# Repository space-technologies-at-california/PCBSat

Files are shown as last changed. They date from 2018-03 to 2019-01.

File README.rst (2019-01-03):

=============
PCB Satellite
=============
Space Technologies at Cal (https://stac.berkeley.edu)

University of California, Berkeley

Getting Started
===============
Clone this repository. Then:

Eagle
-----
#. Obtain the `STAC Eagle library <https://github.com/space-technologies-at-california/electronics>`_ by running::
   
    git submodule init
    git submodule update

#. `Add the library to Eagle <https://www.instructables.com/id/Adding-a-Library-to-Eagle-CAD/>`_.

Firmware
--------
#. Install `MSP430-GCC <http://www.ti.com/tool/msp430-gcc-opensource>`_ and
   `MSPDebug <https://dlbeer.co.nz/mspdebug/>`_.

#. In *firmware/*, make a new file called *msp430.mk.inc* and specify the path
   to your MSP430-GCC installation. For example::

    MSP430_TOOLCHAIN=/usr/local/gcc-msp430-ti-toolchain-5.01.02.00

#. Run ``make`` from *firmware/* to build all firmware configurations. To
   build a specific configuration, change to the appropriate subdirectory (for
   example, *debug/*) and run ``make``. If ``make`` complains about a missing
   *gitrev.h*, type ``make gitrev.h`` and re-run.

#. To change a build configuration, edit *config.h* in the appropriate
   subdirectory.

Programming
~~~~~~~~~~~
#. Obtain a programmer. We use the MSP430F5529 LaunchPad to program our sprite
   using Spy-Bi-Wire (SBW), but any SBW-compatible programmer should work.

#. Disconnect the 5V, 3V, GND, SBW RST and TST jumpers from the LaunchPad.

#. Connect the 3V, GND, SBW RST and TST jumpers on the ezFET-lite side to the
   target.

#. Run ``make prog`` to program, and run ``make verify`` to read back what was
   programmed.

Simulation
----------
Dependencies: igrf12 (https://github.com/scivision/igrf12)

#. Run ``python3 pull_iss_locdata.py``. This will collect (timestamp, latitude,longitude) data of the ISS for 9 hours at 10 second increments. This will create an output file in the current directory titled ``iss_loc_data_{timestamp}.csv``.  
#. Run ``python3 data_gen.py -f iss_loc_data_{timestamp}.csv`` where timestamp corresponds to the file created in the previous step. This will create an output file in the current directory that contains magnetometer data (x,y,z), gyrometer data (x,y,z), and the expected axis and power that the PCBSat should rotate along in addition to the file's previous contents. This output file will be titled ``full_{timestamp}.csv``. The units for the magnetometer data are Gauss and the units for the gyrometer data are radians/second.  

The models for predicting power and axis are still in progress. 

To run tensorboard, navigate to /simulations/python/ and execute `tensorboard --logdir="tmp/model/"`. Make sure that you have the most recent versions of tensorflow and tensorboard installed. 

Directory Structure
===================
- ./eagle : Contains all necessary Eagle files for the sprite board

  - ./eagle/sprite-test: Contains the version of the sprite manufacture by 
    Bay Area Circuits as a test board. It is largely based on the sprite
    verison created by Zac Manchester here: https://github.com/kicksat/sprite

  - ./eagle/final-sprite: Contains the version of the sprite we are currently
    working on. Our sprite began from the attitude-sprite designed by Zac
    Mancherster here: https://github.com/kicksat/attitude-sprite

  - ./eagle/electronics: STAC Eagle library submodule. See Eagle_. Please add
    any parts to the stac.lbr file contained there.
    
- ./simulation : Contains all the simulation netlists and other data 

- ./firmware : Contains all the firmware for the sprite

- ./gerbers : Contains the gerbers for the sprites. 

`Getting Started with Sprite Development Kit <https://github.com/kicksat/sprite/wiki/Getting-started-with-the-Sprite-Development-Kit>`_

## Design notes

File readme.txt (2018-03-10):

PCB Satellite
Space Technologies at Cal
University of California, Berkeley

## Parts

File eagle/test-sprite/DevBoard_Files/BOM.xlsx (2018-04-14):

Part | Value | Device | Package | Desicription | DigiKey Part Number | Manufacturer Part Number | Price | Link
C1 | 27pF | CAP0603-CAP | 0603-CAP | Capacitor | 399-1054-1-ND | C0603C270J5GACTU
C2 | 27pF | CAP0603-CAP | 0603-CAP | Capacitor | 399-1054-1-ND | C0603C270J5GACTU
C3 | 470nF | CAP0603-CAP | 0603-CAP | Capacitor | 399-3114-1-ND | C0603C474K8PACTU
C4 | 470nF | CAP0603-CAP | 0603-CAP | Capacitor | 399-3114-1-ND | C0603C474K8PACTU
C5 | 2.2nF | CAP0603-CAP | 0603-CAP | Capacitor | 399-1085-1-ND | C0603C222K5RACTU
C6 | 100nF | CAP0603-CAP | 0603-CAP | Capacitor | 399-5089-1-ND | C0603C104K5RACTU
C7 | 10nF | CAP0603-CAP | 0603-CAP | Capacitor | 399-1091-1-ND | C0603C103K5RACTU
C8 | 2.2nF | CAP0603-CAP | 0603-CAP | Capacitor | 399-1085-1-ND | C0603C222K5RACTU
C9 | 100nF | CAP0603-CAP | 0603-CAP | Capacitor | 399-5089-1-ND | C0603C104K5RACTU
C10 | 10nF | CAP0603-CAP | 0603-CAP | Capacitor | 399-1091-1-ND | C0603C103K5RACTU
C11 | 100nF | CAP0603-CAP | 0603-CAP | Capacitor | 399-5089-1-ND | C0603C104K5RACTU
C12 | 220nF | CAP0603-CAP | 0603-CAP | Capacitor | 399-1102-1-ND | C0603C224Z4VACTU
C13 | 4.7uF | CAP0603-CAP | 0603-CAP | Capacitor | 399-3482-1-ND | C0603C475K9PACTU
L1 | 12nH | INDUCTOR | 0603-INDUCTOR | Inductor | 587-1546-1-ND | HK160812NJ-T
LED1 | LED0603 | LED-0603 | 0603-LED | Chip LED | 475-2709-1-ND | LG L29K-G2J1-24-Z
R1 | 56K | RESISTOR0603-RES | 0603-RES | Resistor | P56.0KHCT-ND | ERJ-3EKF5602V
R2 | 47K | RESISTOR0603-RES | 0603-RES | Resistor | P47.0KHCT-ND | ERJ-3EKF4702V
R3 | 4.7K | RESISTOR0603-RES | 0603-RES | Resistor | P4.70KHCT-ND | ERJ-3EKF4701V
R4 | 4.7K | RESISTOR0603-RES | 0603-RES | Resistor | P4.70KHCT-ND | ERJ-3EKF4701V
R5 | 270R | RESISTOR0603-RES | 0603-RES | Resistor | P270GCT-ND | ERJ-3GEYJ271V
R6 | 0R | RESISTOR0805-RES | 0805-RES | Resistor | P0.0ACT-ND | ERJ-6GEY0R00V
R7 | 0R | RESISTOR0805-RES | 0805-RES | Resistor | P0.0ACT-ND | ERJ-6GEY0R00V
S1 | TASC | TASC | TASC | Triangular Advanced Solar Cell | N/A | N/A
S2` | TASC | TASC | TASC | Triangular Advanced Solar Cell | N/A | N/A
U1 | CC430F5137 | CC430F513X---RGZ48 | QFN-48 | MSP430 w/ Integrated Radio | 296-27420-1-ND | CC430F5137IRGZR | 6.59 | https://www.digikey.com/products/en?keywords=296-27420-1-ND
U2 | HMC5883LSMD | MMC5883MA | 16-LGA | 3-Axis Digital Compass | 1267-1072-1-ND | MMC5883MA | 5.47 | https://www.digikey.com/product-detail/en/memsic-inc/MMC5883MA/1267-1072-1-ND/7063085
U3 | ITG-3200 | ITG-3200 | QFN-24 | 3-Axis Gyroscope | 37T8091 (Newark) | ITG-3200 | 14.45 | http://www.newark.com/invensense/itg-3200/gyroscope-mems-triple-axis-qfn/dp/37T8091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
X1 | 26MHz | ABM11-XTAL | ABM11_CERAMIC_SMD_CRYSTALABM11 | Quartz Crystal | 535-9815-1-ND | ABM11-26.000MHZ-B7G-T | 1.68 | https://www.digikey.com/products/en?keywords=535-9815-1-ND
JP1 | DNP | Fair-Rite Ferrite Rod | n/a | Ferrite Rod | 623-4052077111 (Mouser) | 4052077111 | 0.16 | https://www.mouser.com/ProductDetail/Fair-Rite/4052077111
JP2 | DNP
JP3 | DNP | DNP | DNP | Jumper
JP4 | DNP | DNP | DNP | Jumper
 |  | DNP | DNP | Jumper
 |  | DNP | DNP | Jumper

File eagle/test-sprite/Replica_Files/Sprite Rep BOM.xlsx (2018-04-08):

Reference | Quantity | Manufacturer | Part Number | Package | Description | Type
C1, C2 | 2 | Kemet | C0603C270J5GACTU | 0603 | Cap 27 pF | DNS
C3, C4 | 2 | Kemet | C0603C474K8PACTU | 0603 | Cap 470 nF | SMT
C5 | 1 | Yageo | CC0603KRX7R9BB222 | 0603 | Cap 2.2 nF | SMT
C6 | 1 | Panasonic |  | 0603 | Cap 100 nF | DNS
C7 | 1 | Panasonic |  | 0603 | Cap 10 nF | DNS
L1 | 1 | Taiyo Yuden | HK160812NJ-T | 0603 | Inductor 32 nH | DNS
R1 | 1 | Panasonic | ERJ-3EKF5602V | 0603 | Resistor 56K | SMT
R2 | 1 | Panasonic | ERJ-3EKF4702V | 0603 | Resistor 47K | SMT
R3, R4, R5, R6, R7, R8 | 6 | Panasonic | ERJ-3GEYJ271V | 0603 | Resistor 270R | SMT
D1, D2, D3, D4, D5, D6 | 6 | Osram | LG L29K-G2J1-24-Z | 0603 | LED | SMT
S1 | 1 | Spectrolab |  | TASC | Soalar Cell | DNS
U1 | 1 | Texas Instruments | CC430F5137IRGZR | 48-QFN | MCU/Radio SoC | Fine Pitch
X1 | 1 |  |  | ABM11 | Crystal 26MHz | DNS

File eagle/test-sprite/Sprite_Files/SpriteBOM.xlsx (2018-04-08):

Part | Quantity | Value | Device | Package | Description | DigiKey Part Number
C1, C5, C7 | 3 | 10 nF | CAP0603-CAP | 0603-CAP | CAP CER 10000PF 50V X7R 0603 | 399-1091-1-ND
C2, C3 | 2 | 470nF | CAP0603-CAP | 0603-CAP | CAP CER 0.47UF 10V X5R 0603 | 399-3114-1-ND
C4 | 1 | 2.2nF | CAP0603-CAP | 0603-CAP | CAP CER 2200PF 50V X7R 0603 | 399-1085-1-ND
C6, C8, C9 | 3 | 0.1uF | CAP0603-CAP | 0603-CAP | CAP CER 0.1UF 50V X7R 0603 | 399-5089-1-ND
C10 | 1 | 10uF | CAP0603-CAP | 0603-CAP | CAP CER 10UF 10V X5R 0603 | 490-10475-1-ND
D1 | 1 | LED | LED0603-LED | 0603-LED | LED GREEN DIFFUSED 0603 SMD | 475-2709-1-ND
L1 | 1 | 12 nH | INDUCTOR0603 | 0603-IND | FIXED IND 12NH 300MA 280 MOHM | 587-1546-1-ND
P1, P2 | 2 | SPRITE_PIN | SPRITE_PIN | SPRITE_PIN | TESTPOINT PIN SMD | ED1088CT-ND
R1 | 1 | 56K | RESISTOR0603-RES | 0603-RES | RES SMD 56K OHM 1% 1/10W 0603 | P56.0KHCT-ND
R2 | 1 | 47K | RESISTOR0603-RES | 0603-RES | RES SMD 47K OHM 1% 1/10W 0603 | P47.0KHCT-ND
R3, R4, R6, R7 | 4 | 0R | RESISTOR0805-RES | 0805-RES | RES SMD 0.0 OHM JUMPER 1/8W 0805 | P0.0ACT-ND
R5 | 1 | 270R | RESISTOR0603-RES | 0603-RES | RES SMD 270 OHM 5% 1/10W 0603 | P270GCT-ND
S1, S2, S3, S4 | 4 | TRISOLX-WING | TRISOLX-WING | TRISOLX-T01 | Solar Cell TRISOLX | N/A
U1 | 1 | CC430F5137 | CC430F513X---RGZ48 | RGZ48 | IC MCU 16B 32K W/RF CORE 48VQFN | 296-38903-2-ND
U2 | 1 | LSM9DS1 | LSM9DS1 | LGA24-8X4 | ACCELEROMETER 3D INEMO 24TFLGA | 497-14946-1-ND
X1 | 1 | TCXO_7Z | TCXO_7Z | TXC_7Z | OSC TCXO 26.000MHZ CLPD SNWV SMD | 887-1622-1-ND

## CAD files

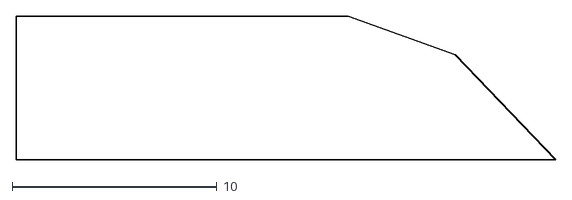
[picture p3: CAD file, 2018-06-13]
mechanical/TrisolX RS.dxf
26.4 x 7.04

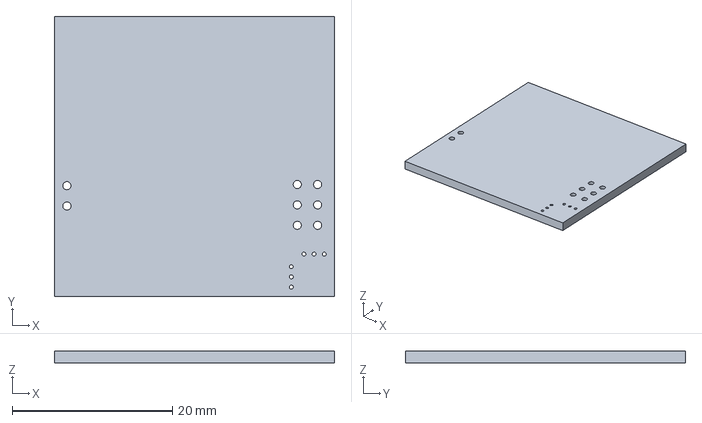
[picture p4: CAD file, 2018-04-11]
mechanical/DevBoard_stp.step
35.0 x 35.0 x 1.55 mm

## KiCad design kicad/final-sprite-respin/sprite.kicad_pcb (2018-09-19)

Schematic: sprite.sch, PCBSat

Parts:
A1, A2: SPRITEANTENNA_ANTENNA
C1, C7: 470n; C0402
C2: 2.2n; C0402
C3, C5, C15: 0.1u; C0402
C4, C6, C9, C11: 10n; C0402
C8, C12, C16, C17: 10u; C0402
C10, C18, C19, C20, C21, C22, C23, C24, C25, C26, C27, C28, C29, C30, C31, C32, C33: CPH3225A; CAPCP3225X100N
C13, C14: 4.7u; C0402
J1: M20-7910442R
L1: LPS4018-223M
L2: 12 nH; 0603
L3, L4: PCBSAT-TORQUECOIL
LED1: LED0603; LED-0603
MK1: Mounting_Hole
R1: 43K; R0402
R2: 270R; R0402
R3, R5, R6: 10K; R0402
R4: 56K; R0402
R7: 150K; R0402
R8: 1M; R0402
R9: 7K; R0402
R10: 200k; R0402
R11, R12, R22: 15R; R0402
R13, R14: OPT; R0402
R15: 5.49M; R0402
R16: 453K; R0402
R17: 4.53M; R0402
R18, R19: 5M; R0402
R20: 4.42M; R0402
R21: 5.6M; R0402
U1: CC430F513X; TI_MSP430_V16_RGZ48
U2: LSM9DS1; LGA24-8X4
U3: SPRITETCXO_TCXO_7Z; SPRITETCXO_TXC_7Z
U4, U6, U7: DRV8837; SON50P200X200X75-8N
U5: ADP5092; QFN50P400X400X100-25N
U8, U9: TASC
X1, X2: SPRITEPIN_SPRITE_PIN

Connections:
/DRDY: U1.11, U2.9
/DSW: U1.24, U5.22
/EN_1: U1.43, U4.7
/EN_2: U1.44, U6.7
/EN_3: U1.48, U7.7
/INT1: U1.4, U2.11
/INT2: U1.3, U2.12
/PGOOD: U1.12, U5.19
/PWM1: U1.1, U4.6, U6.6, U7.6
/PWM2: U1.2, U4.5, U6.5, U7.5
/REF: R15.2, R18.2, R20.2, U5.1
/REGGOOD: U1.37, U5.11
/REG_D0: U1.13, U5.24
/REG_D1: U1.15, U5.23
/RF_N: A1.IN1, A1.IN2, A1.IN3, U1.30
/RF_P: A2.IN1, A2.IN2, A2.IN3, U1.29
/SCL: R3.2, U1.9, U2.2
/SDA: R5.2, U1.10, U2.4
/SETHYS: R16.1, R17.2, U5.6
/SETPG: R15.1, R16.2, U5.5
/SETSD: R18.1, R19.2, U5.2
/SPIRAL: R22.1, U7.2
/SWN: L1.P$2, U5.13
/TERM: R20.1, R21.2, U5.4
/TST: J1.3, U1.39
/UART_RX: J1.5, U1.6
/UART_TX: J1.4, U1.5
/VBAT: C10.1 (+), C18.1 (+), C19.1 (+), C20.1 (+), C21.1 (+), C22.1 (+), C23.1 (+), C24.1 (+), C25.1 (+), C26.1 (+), C27.1 (+), C28.1 (+), C29.1 (+), C30.1 (+), C31.1 (+), C32.1 (+), C33.1 (+), U5.17
/VCORE: C1.1, U1.7
/~RST: C2.2, J1.2, R1.2, U1.40
GND: C1.2, C2.1, C3.2, C4.2, C5.2, C7.2, C8.2, C9.2, C10.2 (-), C11.2, C12.2, C13.2, C14.2, C15.2, C16.2, C17.2, C18.2 (-), C19.2 (-), C20.2 (-), C21.2 (-), C22.2 (-), C23.2 (-), C24.2 (-), C25.2 (-), C26.2 (-), C27.2 (-), C28.2 (-), C29.2 (-), C30.2 (-), C31.2 (-), C32.2 (-), C33.2 (-), J1.6, LED1.C, R4.2, R8.1, R9.2, R10.1, R17.1, R19.1, R21.1, U1.42, U1.TP, U2.14, U2.15, U2.16, U2.17, U2.18, U2.19, U2.20, U3.GND1, U3.GND2, U4.4, U4.9, U5.3, U5.7, U5.12, U5.25, U6.4, U6.9, U7.4, U7.9, U8.MINUS1, U8.MINUS2, U9.MINUS1, U9.MINUS2, X2.PIN
unnamed: C4.1, U2.21
unnamed: C5.1, U2.24
unnamed: C6.1, U1.25
unnamed: C6.2, U3.OUT
unnamed: C9.1, U5.8
unnamed: L3.1, U4.3
unnamed: L3.2, R11.2
unnamed: L4.1, R12.2
unnamed: L4.2, U6.3
unnamed: LED1.A, R2.2
unnamed: R2.1, U1.14
unnamed: R4.1, U1.33
unnamed: R6.2, U2.5, U2.6, U2.7, U2.8, U2.13
unnamed: R7.1, R8.2, U5.9
unnamed: R9.1, U5.20
unnamed: R10.2, U5.21
unnamed: R11.1, U4.2
unnamed: R12.1, U6.2
unnamed: R22.2, U7.3
VCC: C3.1, C14.1, C15.1, J1.1, L2.1, R1.1, R3.1, R5.1, R6.1, R13.2, R14.1, U1.8, U1.22, U1.41, U1.45, U2.1, U2.3, U2.22, U2.23, U4.8, U5.16, U6.8, U7.8, X1.PIN
VCCA: C7.1, C11.1, L2.2, U1.27, U1.28, U1.31, U1.32, U1.34, U3.VCC
VCCINT: C17.1, L1.P$1, R7.2, R14.2, U5.10, U8.PLUS, U9.PLUS
VCCIO: C8.1, C12.1, C13.1, C16.1, R13.1, U4.1, U5.14, U5.15, U6.1, U7.1

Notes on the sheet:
Sensing:
CORE:
Torque Coils
Power
REG_OUT = VCCIO = 1.5V (see Table 7) VSYS = VBAT = 2.2-2.7V
16 V
1% REQ
All Caps 3.3V Except C21 (16V) All Passives 0402 All Passives (5%) Except R4, R15 - R21 (1%) Subject to Change R2, R11, R12, R22 R7, R8 C3 MPPT Max efficiency: R7/(R7 + R8) = 87% Vsetsd: 1V*(1+R18/R19) = 2V Vbat_term: (3/2)V*(1+R20/R21) = 2.7V Vsetpg_falling: 1V*(1+(R15/(R16+R17))) = 2.102V Vsetpg_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
Design Notes
PCB Spiral Inductor Layers 2 and 3

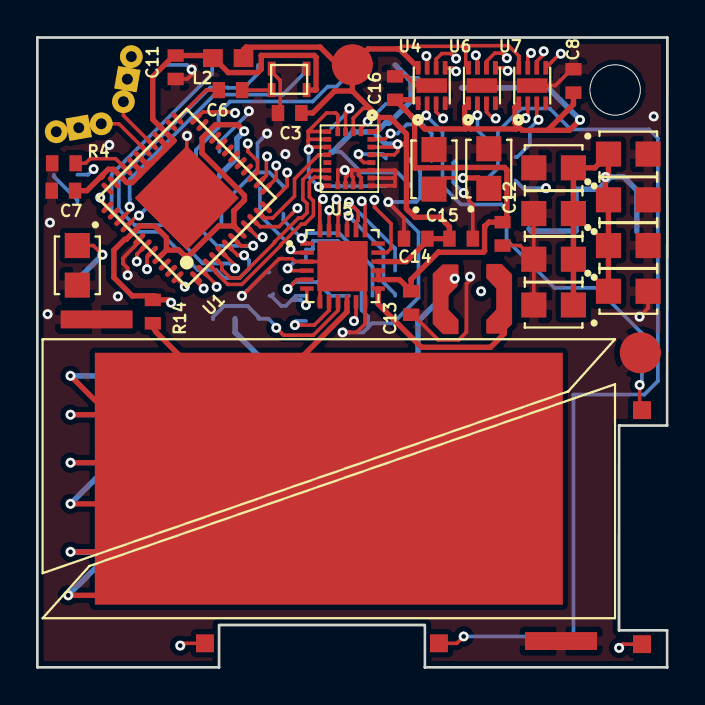
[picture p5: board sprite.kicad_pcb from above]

Board: 4 copper layers, 35.0 x 35.0 mm, 75 parts (0 on the bottom side), 54 nets.

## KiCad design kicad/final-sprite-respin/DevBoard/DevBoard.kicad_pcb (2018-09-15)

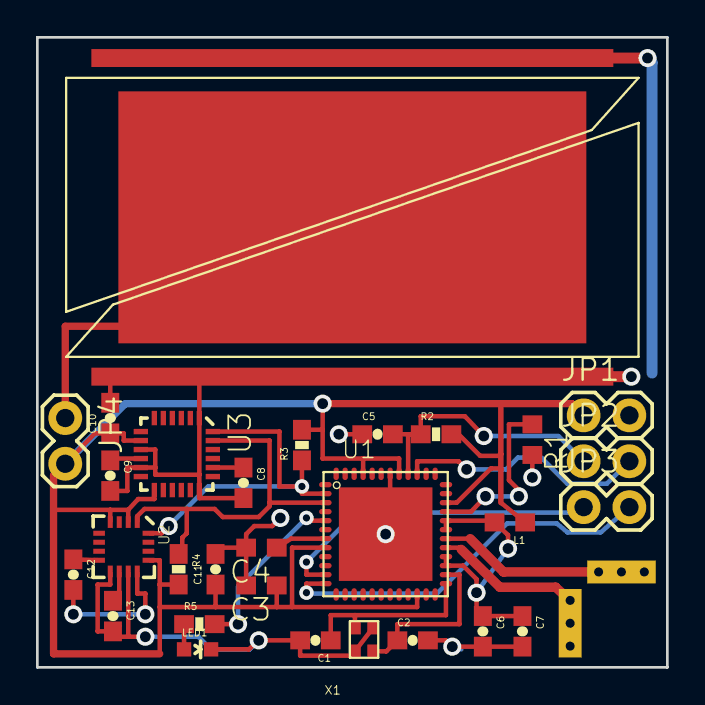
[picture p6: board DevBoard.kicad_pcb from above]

Board: 16 copper layers, 35.0 x 35.0 mm, 31 parts (0 on the bottom side), 23 nets.

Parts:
ANT-N1: ANTENNA
ANT-P1: ANTENNA
C1, C2: 27pF; 0603-CAP
C3, C4: 470nF; C0603
C5, C8: 2.2nF; 0603-CAP
C6, C9, C11: 100nF; 0603-CAP
C7, C10: 10nF; 0603-CAP
C12: 220nF; 0603-CAP
C13: 4.7uF; 0603-CAP
JP1, JP2, JP3, JP4: M02PTH; 1X02
L1: 12 nH; 0603
LED1: LED0603; LED-0603
R1: 56K; R0603
R2: 47K; 0603-RES
R3, R4: 4.7K; 0603-RES
R5: 270R; 0603-RES
S1: TASC
U1: CC430F5137; RGZ48
U2: HMC5883LSMD; 16LPCC
U3: ITG-3200; QFN-24
X1: 26 MHz; ABM11_CERAMIC-SMD-CRYSTAL

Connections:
/SCL: R4.1, U1.3, U2.1, U3.23
/SDA: R3.1, U1.2, U2.16, U3.24
GND: C1.2, C2.2, C3.2, C4.2, C5.1, C6.2, C7.2, C8.2, C9.2, C10.2, C11.2, C13.2, JP1.2, LED1.C, R1.2, S1.MINUS1, S1.MINUS2, U1.42, U1.TP, U2.9, U2.11, U3.1, U3.9, U3.11, U3.18, X1.P$2, X1.P$4
unnamed: ANT-N1.IN1, ANT-N1.IN2, ANT-N1.IN3, U1.30
unnamed: ANT-P1.IN1, ANT-P1.IN2, ANT-P1.IN3, U1.29
unnamed: C1.1, U1.25, X1.P$1
unnamed: C2.1, U1.26, X1.P$3
unnamed: C4.1, U1.7
unnamed: C5.2, JP2.1, R2.1, U1.40
unnamed: C6.1, C7.1, L1.2, U1.27, U1.28, U1.31, U1.32
unnamed: C8.1, U3.20
unnamed: C9.1, U3.10
unnamed: C12.1, U2.8
unnamed: C12.2, U2.12
unnamed: C13.1, U2.10
unnamed: JP2.2, U1.39
unnamed: JP3.1, U1.11
unnamed: JP3.2, U1.12
unnamed: JP4.1, S1.PLUS
unnamed: LED1.A, R5.1
unnamed: R1.1, U1.33
unnamed: R5.2, U1.5
VCC: C3.1, C10.1, C11.1, JP1.1, JP4.2, L1.1, R2.2, R3.2, R4.2, U1.8, U1.22, U1.34, U1.41, U1.45, U2.2, U2.4, U2.13, U3.8, U3.13

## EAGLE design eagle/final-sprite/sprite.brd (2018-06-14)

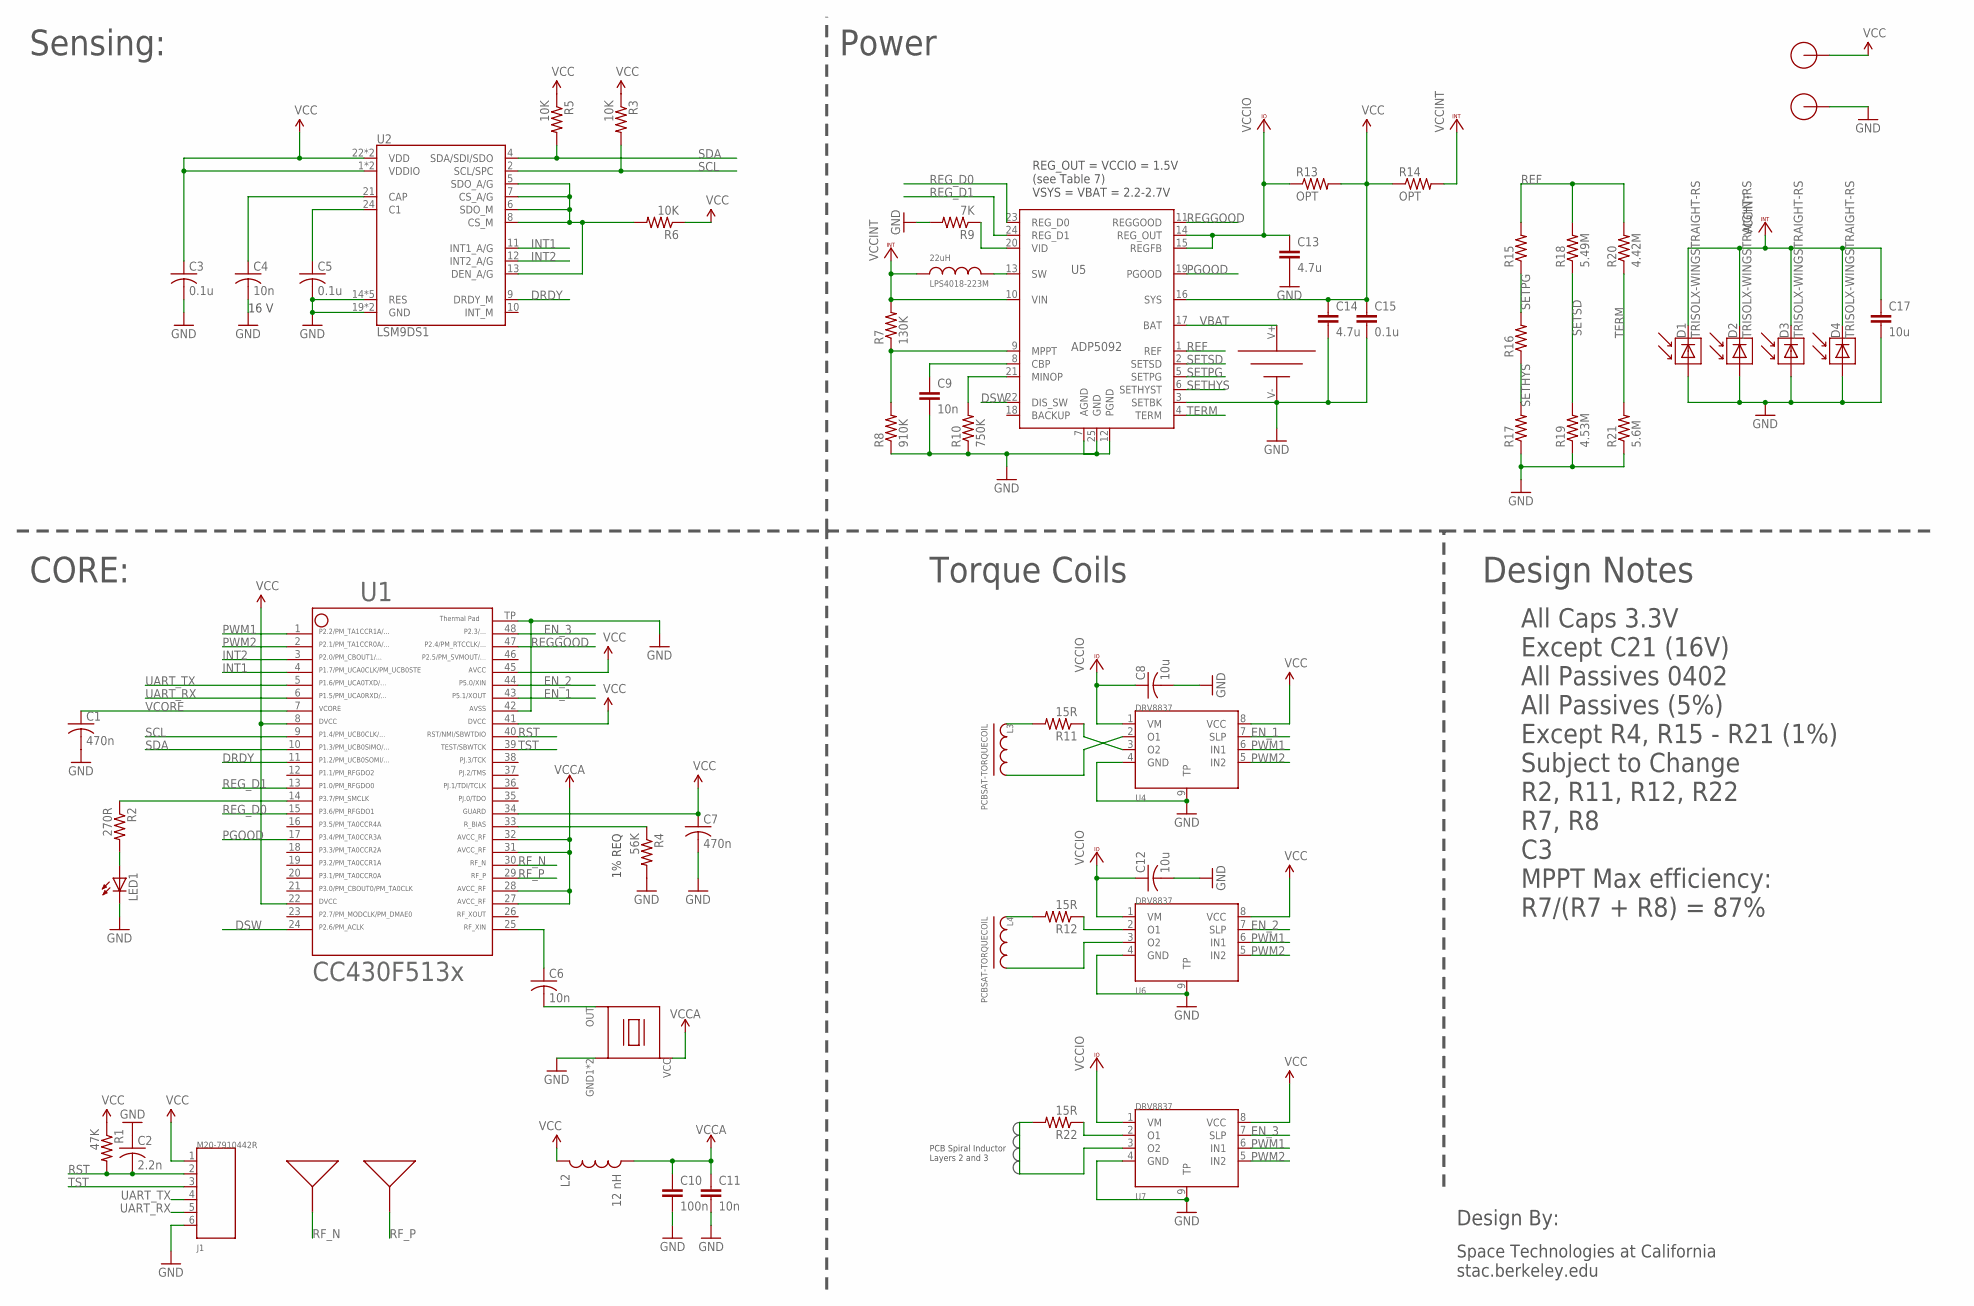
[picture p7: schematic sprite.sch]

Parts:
A1, A2: SPRITEANTENNA_ANTENNA
B1: UMAC_UMAC
C1, C7: 470n; C0402
C2: 2.2n; C0402
C3, C5, C15: 0.1u; C0402
C4, C6, C9, C11: 10n; C0402
C8, C12, C17: 10u; C0402
C10: 100n; C0402
C13, C14: 4.7u; C0402
D1, D2, D3, D4: TRISOLX-WINGSTRAIGHT-RS; TRISOLX-STRAIGHT-RS
J1: M20-7910442R
L1: LPS4018-223M
L2: 12 nH; 0603
L3, L4: PCBSAT-TORQUECOIL
LED1: LED0603; LED-0603
R1: 47K; R0402
R2: 270R; R0402
R3, R5, R6: 10K; R0402
R4: 56K; R0402
R7: 130K; R0402
R8: 910K; R0402
R9: 7K; R0402
R10: 750K; R0402
R11, R12, R22: 15R; R0402
R13, R14: OPT; R0402
R15, R16, R17: R-US_R0402; R0402
R18: 5.49M; R0402
R19: 4.53M; R0402
R20: 4.42M; R0402
R21: 5.6M; R0402
U1: CC430F513X; TI_MSP430_V16_RGZ48
U2: LSM9DS1; LGA24-8X4
U3: SPRITETCXO_TCXO_7Z; SPRITETCXO_TXC_7Z
U4, U6, U7: DRV8837; SON50P200X200X75-8N
U5: ADP5092; QFN50P400X400X100-25N
X1, X2: SPRITEPIN_SPRITE_PIN

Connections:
DRDY: U1.11, U2.9 (DRDY_M)
DSW: U1.24, U5.22 (DIS_SW)
EN_1: U1.43, U4.7 (SLP)
EN_2: U1.44, U6.7 (SLP)
EN_3: U1.48, U7.7 (SLP)
GND: B1.V-, C1.2, C2.1, C3.2, C4.2, C5.2, C7.2, C8.2, C9.2, C10.2, C11.2, C12.2, C13.2, C14.2, C15.2, C17.2, D1.P$1 (A), D2.P$1 (A), D3.P$1 (A), D4.P$1 (A), J1.6, LED1.C, R4.2, R8.1, R9.2, R10.1, R17.1, R19.1, R21.1, U1.42, U1.TP (49), U2.14 (RES), U2.15 (RES), U2.16 (RES), U2.17 (RES), U2.18 (RES), U2.19 (GND), U2.20 (GND), U3.GND1 (GND), U3.GND2 (GND), U4.4 (GND), U4.9 (TP), U5.3 (SETBK), U5.7 (AGND), U5.12 (PGND), U5.25 (GND), U6.4 (GND), U6.9 (TP), U7.4 (GND), U7.9 (TP), X2.PIN
INT1: U1.4, U2.11 (INT1_A/G)
INT2: U1.3, U2.12 (INT2_A/G)
unnamed: C6.1, U1.25
unnamed: R2.1, U1.14
unnamed: R4.1, U1.33
unnamed: L3.1, R11.2
unnamed: C5.1, U2.24 (C1)
unnamed: C4.1, U2.21 (CAP)
unnamed: R6.2, U2.5 (SDO_A/G), U2.6 (SDO_M), U2.7 (CS_A/G), U2.8 (CS_M), U2.13 (DEN_A/G)
unnamed: R11.1, U4.3 (O2)
unnamed: L4.1, R12.2
unnamed: LED1.A, R2.2
unnamed: C6.2, U3.OUT
unnamed: R22.1, U7.2 (O1)
unnamed: L3.2, U4.2 (O1)
unnamed: R9.1, U5.20 (VID)
unnamed: R7.1, R8.2, U5.9 (MPPT)
unnamed: R10.2, U5.21 (MINOP)
unnamed: C9.1, U5.8 (CBP)
unnamed: L1.P$2, U5.13 (SW)
unnamed: R12.1, U6.2 (O1)
unnamed: L4.2, U6.3 (O2)
unnamed: R22.2, U7.3 (O2)
PGOOD: U1.17, U5.19 (PGOOD)
PWM1: U1.1, U4.6 (IN1), U6.6 (IN1), U7.6 (IN1)
PWM2: U1.2, U4.5 (IN2), U6.5 (IN2), U7.5 (IN2)
REF: R15.2, R18.2, R20.2, U5.1 (REF)
REGGOOD: U1.47, U5.11 (REGGOOD)
REG_D0: U1.15, U5.23 (REG_D0)
REG_D1: U1.13, U5.24 (REG_D1)
RF_N: A1.IN1, A1.IN2, A1.IN3, U1.30
RF_P: A2.IN1, A2.IN2, A2.IN3, U1.29
RST: C2.2, J1.2, R1.2, U1.40
SCL: R3.2, U1.9, U2.2 (SCL/SPC)
SDA: R5.2, U1.10, U2.4 (SDA/SDI/SDO)
SETHYS: R16.1, R17.2, U5.6 (SETHYST)
SETPG: R15.1, R16.2, U5.5 (SETPG)
SETSD: R18.1, R19.2, U5.2 (SETSD)
TERM: R20.1, R21.2, U5.4 (TERM)
TST: J1.3, U1.39
UART_RX: J1.5, U1.6
UART_TX: J1.4, U1.5
VBAT: B1.V+, U5.17 (BAT)
VCC: C3.1, C7.1, C14.1, C15.1, J1.1, L2.1, R1.1, R3.1, R5.1, R6.1, R13.2, R14.1, U1.8, U1.22, U1.34, U1.41, U1.45, U2.1 (VDDIO), U2.3 (VDDIO), U2.22 (VDD), U2.23 (VDD), U4.8 (VCC), U5.16 (SYS), U6.8 (VCC), U7.8 (VCC), X1.PIN
VCCA: C10.1, C11.1, L2.2, U1.27, U1.28, U1.31, U1.32, U3.VCC
VCCINT: C17.1, D1.P$2 (C), D2.P$2 (C), D3.P$2 (C), D4.P$2 (C), L1.P$1, R7.2, R14.2, U5.10 (VIN)
VCCIO: C8.1, C12.1, C13.1, R13.1, U4.1 (VM), U5.14 (REG_OUT), U5.15 (REGFB), U6.1 (VM), U7.1 (VM)
VCORE: C1.1, U1.7

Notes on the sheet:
Sensing:
CORE:
Torque Coils
Space Technologies at California stac.berkeley.edu
Design By:
Power
REG_OUT = VCCIO = 1.5V (see Table 7) VSYS = VBAT = 2.2-2.7V
16 V
1% REQ
All Caps 3.3V Except C21 (16V) All Passives 0402 All Passives (5%) Except R4, R15 - R21 (1%) Subject to Change R2, R11, R12, R22 R7, R8 C3 MPPT Max efficiency: R7/(R7 + R8) = 87%
Design Notes
PCB Spiral Inductor Layers 2 and 3

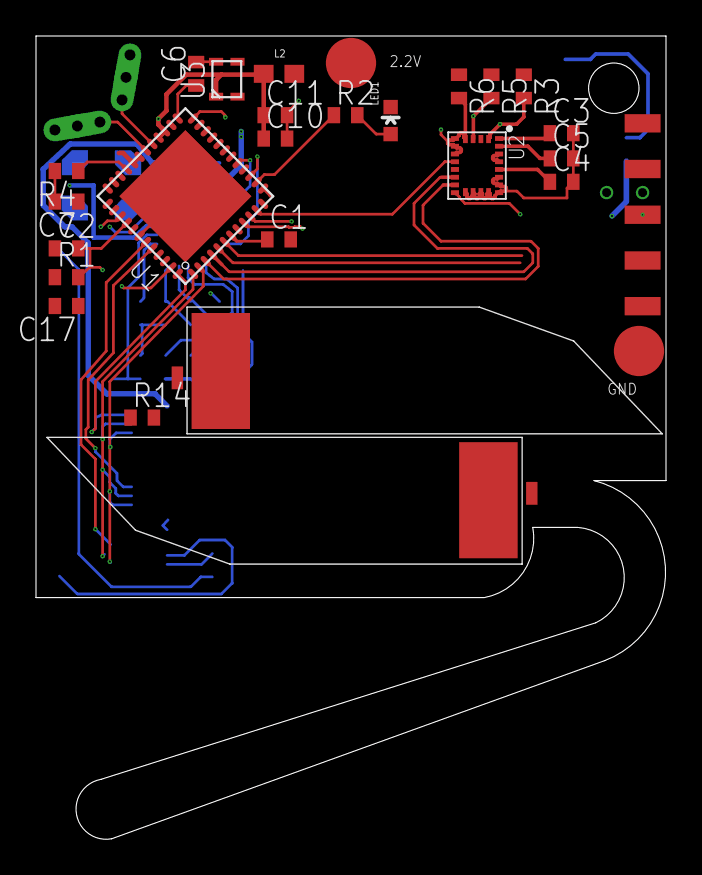
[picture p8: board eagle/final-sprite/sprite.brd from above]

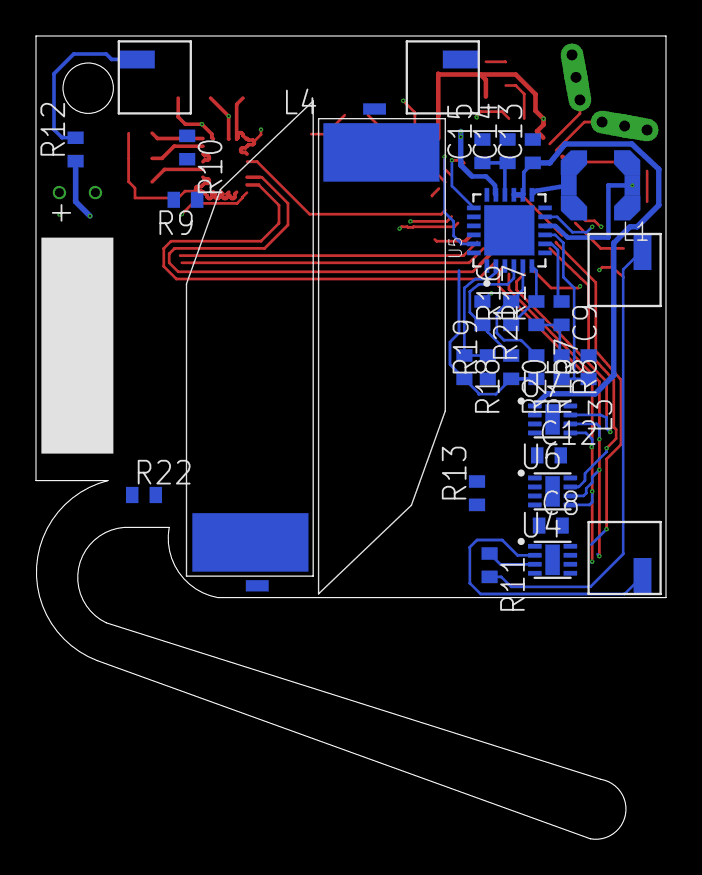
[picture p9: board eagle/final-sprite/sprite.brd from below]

Board: 4 copper layers, 35.0 x 44.6 mm, 60 parts (31 on the bottom side), 54 nets.

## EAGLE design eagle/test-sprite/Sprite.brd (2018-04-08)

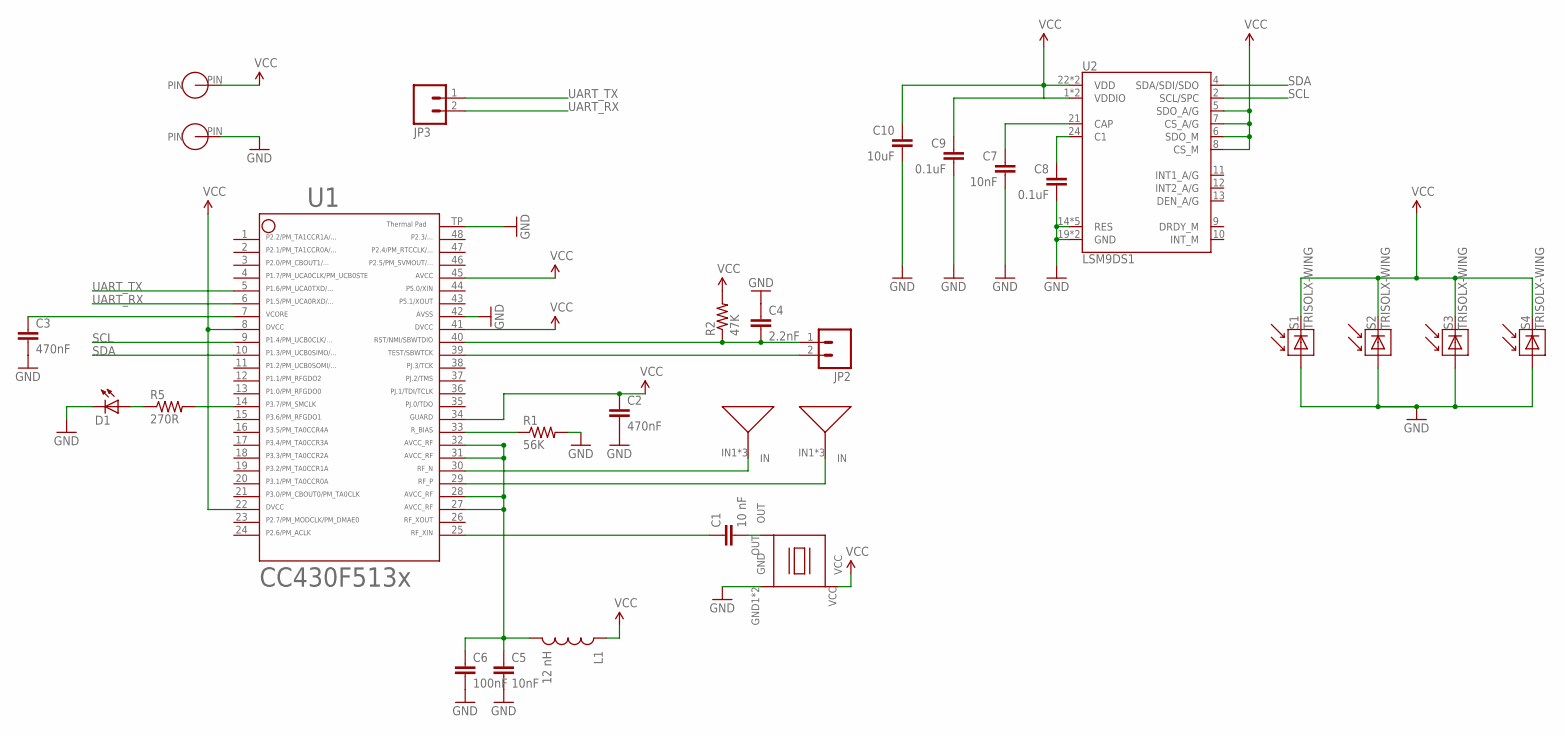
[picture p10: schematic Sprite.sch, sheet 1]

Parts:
ANT-N: ANTENNA
ANT-P: ANTENNA
C1: 10 nF; 0603-CAP
C2, C3: 470nF; 0603-CAP
C4: 2.2nF; 0603-CAP
C5, C7: 10nF; 0603-CAP
C6: 100nF; 0603-CAP
C8, C9: 0.1uF; 0603-CAP
C10: 10uF; 0603-CAP
D1: LED0603; LED-0603
JP2, JP3: M02PTH; 1X02
L1: 12 nH; 0603
P1, P2: SPRITE_PIN
R1: 56K; 0603-RES
R2: 47K; 0603-RES
R5: 270R; 0603-RES
S1, S2, S3, S4: TRISOLX-WING; TRISOLX-T01
U1: CC430F5137; RGZ48
U2: LSM9DS1; LGA24-8X4
X1: TCXO_7Z; TXC_7Z

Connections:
GND: C2.2, C3.2, C4.1, C5.2, C6.2, C7.2, C8.2, C9.2, C10.2, D1.C, P1.PIN, R1.2, S1.P$3 (A), S2.P$3 (A), S3.P$3 (A), S4.P$3 (A), U1.42, U1.TP (49), U2.14 (RES), U2.15 (RES), U2.16 (RES), U2.17 (RES), U2.18 (RES), U2.19 (GND), U2.20 (GND), X1.GND1 (GND), X1.GND2 (GND)
unnamed: C1.1, U1.25
unnamed: R5.2, U1.14
unnamed: R1.1, U1.33
unnamed: C3.1, U1.7
unnamed: C7.1, U2.21 (CAP)
unnamed: C8.1, U2.24 (C1)
unnamed: D1.A, R5.1
unnamed: C1.2, X1.OUT
RFN: ANT-N.IN1, ANT-N.IN2, ANT-N.IN3, U1.30
RFP: ANT-P.IN1, ANT-P.IN2, ANT-P.IN3, U1.29
RST: C4.2, JP2.1, R2.1, U1.40
SCL: U1.9, U2.2 (SCL/SPC)
SDA: U1.10, U2.4 (SDA/SDI/SDO)
TEST: JP2.2, U1.39
UART_RX: JP3.2, U1.6
UART_TX: JP3.1, U1.5
VCC: C2.1, C9.1, C10.1, L1.1, P2.PIN, R2.2, S1.P$2 (C), S2.P$2 (C), S3.P$2 (C), S4.P$2 (C), U1.8, U1.22, U1.34, U1.41, U1.45, U2.1 (VDDIO), U2.3 (VDDIO), U2.5 (SDO_A/G), U2.6 (SDO_M), U2.7 (CS_A/G), U2.8 (CS_M), U2.22 (VDD), U2.23 (VDD), X1.VCC
VCCRF: C5.1, C6.1, L1.2, U1.27, U1.28, U1.31, U1.32

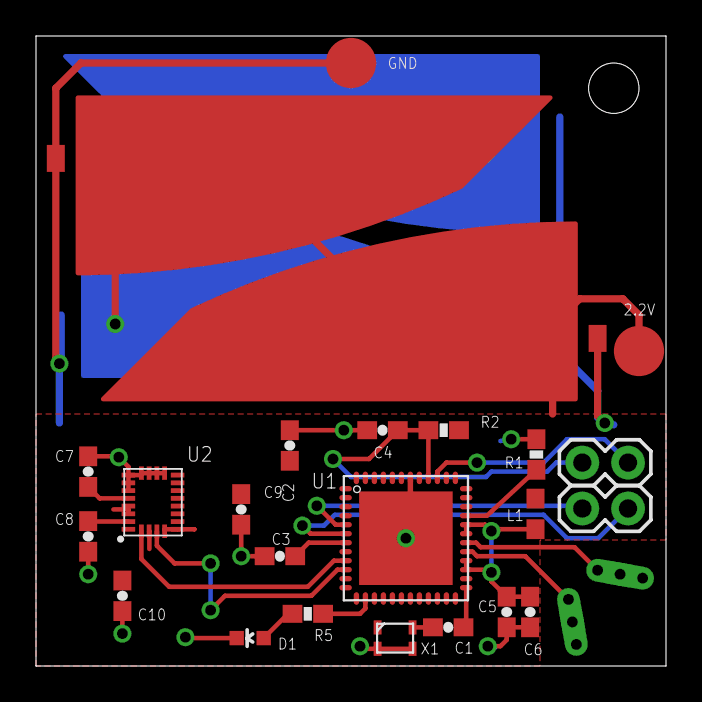
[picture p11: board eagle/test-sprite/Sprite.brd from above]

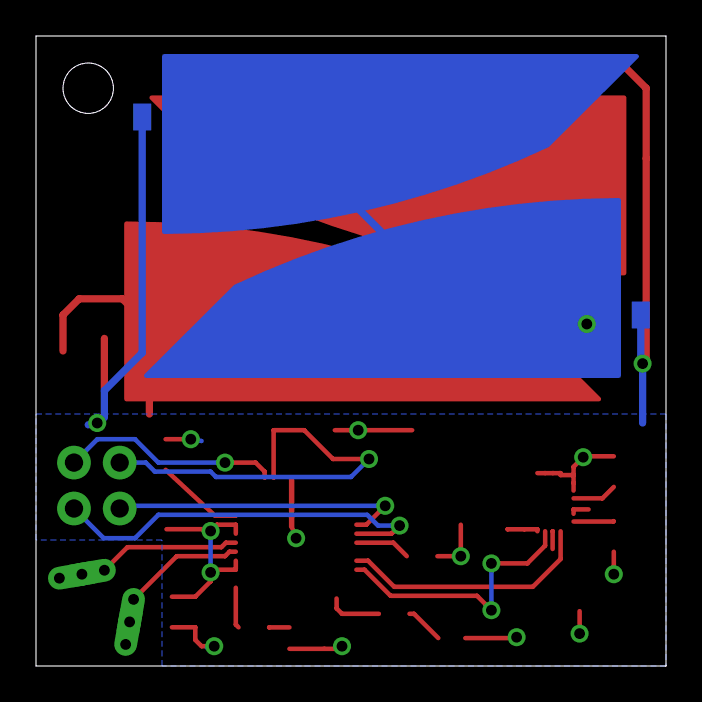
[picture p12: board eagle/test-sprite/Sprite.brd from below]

Board: 2 copper layers, 35.0 x 35.0 mm, 28 parts (2 on the bottom side), 19 nets.

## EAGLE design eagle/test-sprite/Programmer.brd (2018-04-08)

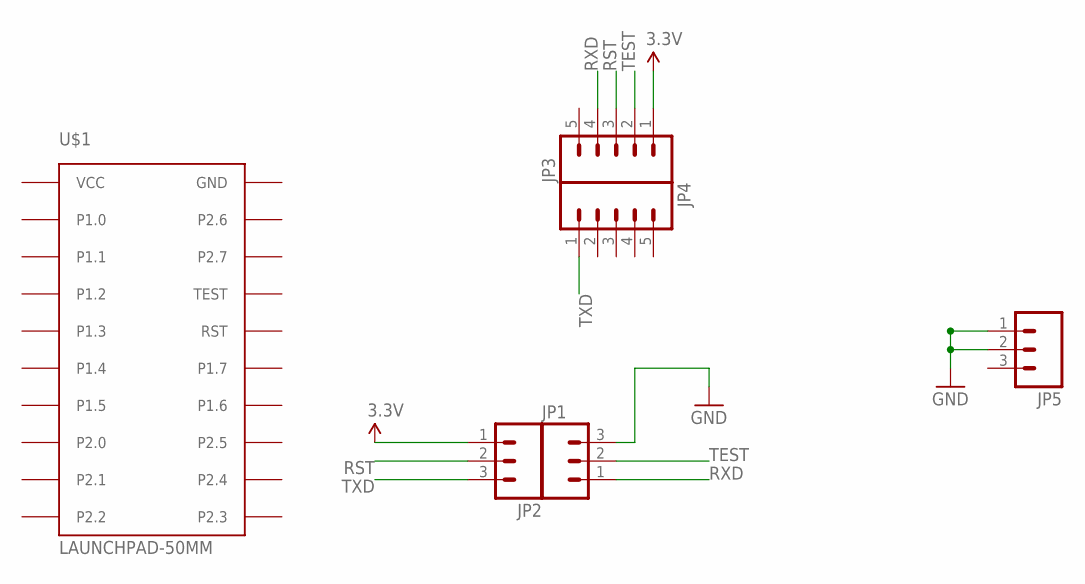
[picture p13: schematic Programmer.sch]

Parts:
JP1, JP2, JP5: M03LOCK; 1X03_LOCK
JP3, JP4: M05LOCK; 1X05_LOCK
U$1: LAUNCHPAD-50MM

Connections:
3.3V: JP2.1, JP3.1
GND: JP1.3, JP5.1, JP5.2, U$1.GND
RST: JP2.2, JP3.3
RXD: JP1.1, JP3.4
TEST: JP1.2, JP3.2
TXD: JP2.3, JP4.1
VCC: U$1.VCC

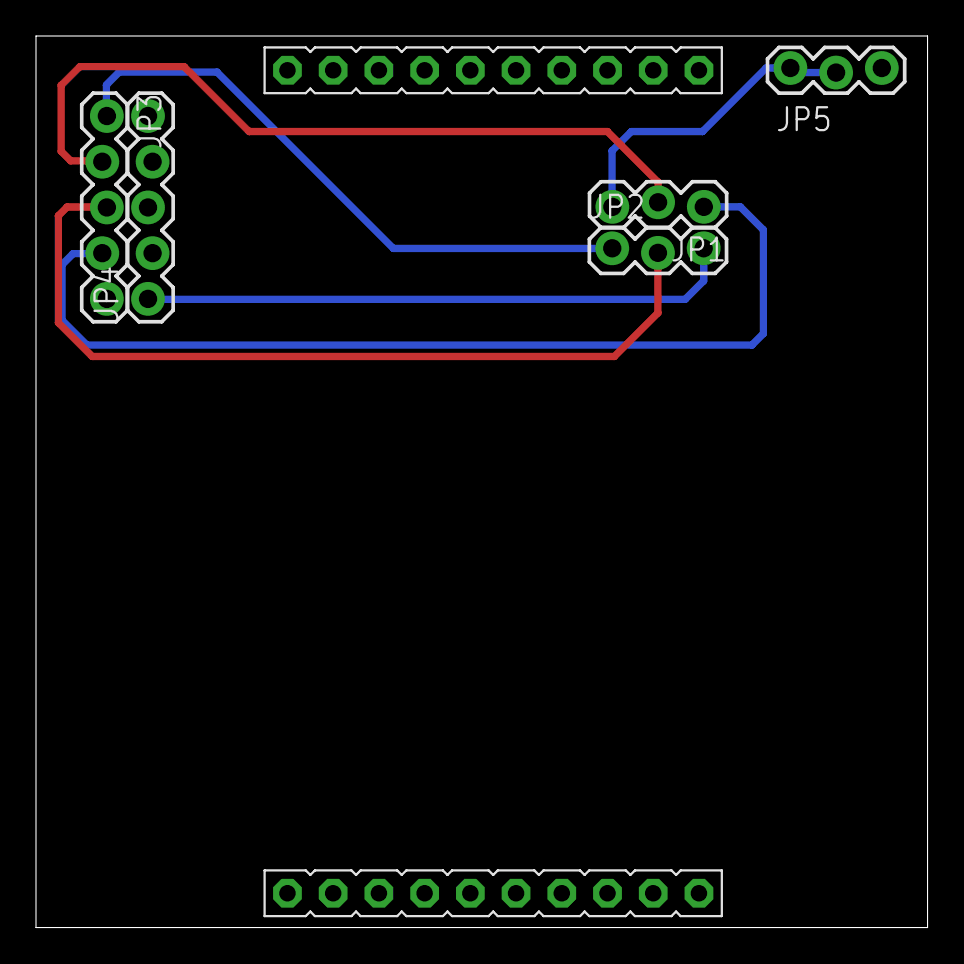
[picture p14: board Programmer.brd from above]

Board: 2 copper layers, 49.5 x 49.5 mm, 6 parts (0 on the bottom side), 6 nets.

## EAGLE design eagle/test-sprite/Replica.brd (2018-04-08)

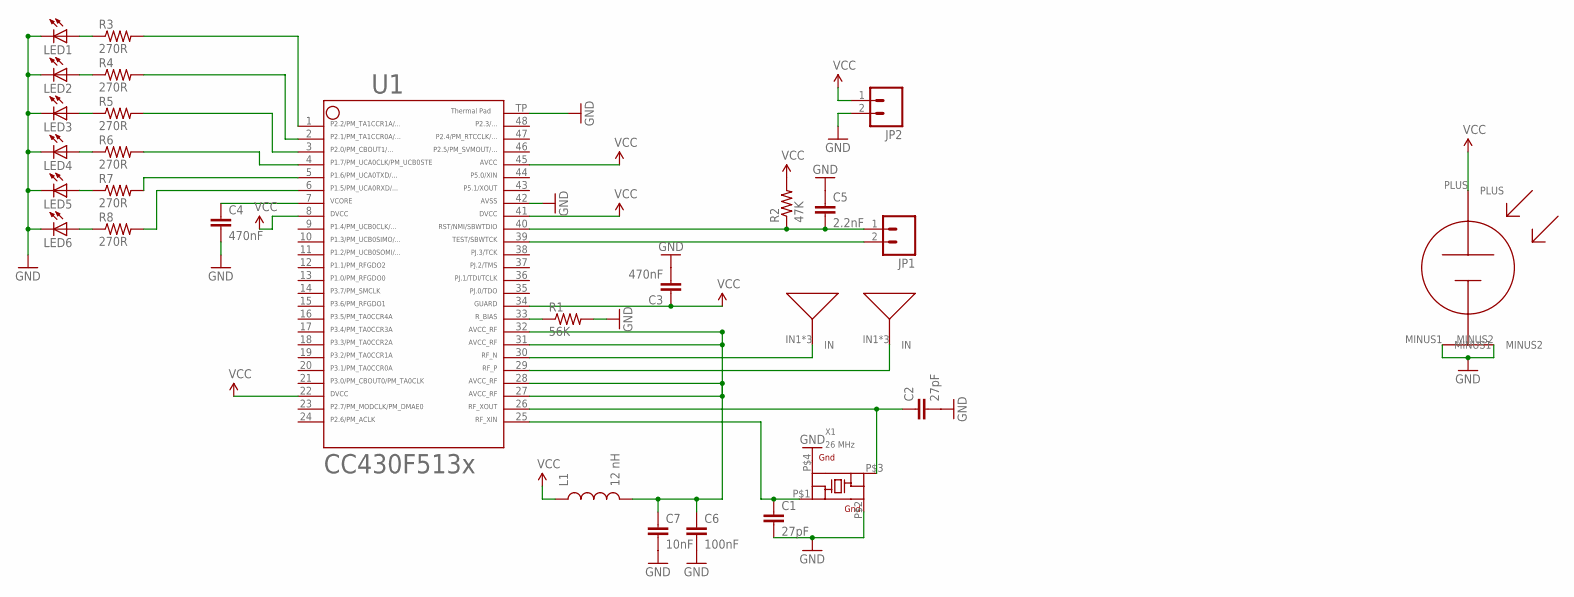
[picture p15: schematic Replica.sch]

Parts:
ANT-N: ANTENNA
ANT-P: ANTENNA
C1, C2: 27pF; 0603-CAP
C3, C4: 470nF; 0603-CAP
C5: 2.2nF; 0603-CAP
C6: 100nF; 0603-CAP
C7: 10nF; 0603-CAP
JP1, JP2: M02PTH; 1X02
L1: 12 nH; 0603
LED1, LED2, LED3, LED4, LED5, LED6: LED0603; LED-0603
R1: 56K; 0603-RES
R2: 47K; 0603-RES
R3, R4, R5, R6, R7, R8: 270R; 0603-RES
S1: TASC
U1: CC430F5137; RGZ48
X1: 26 MHz; ABM11_CERAMIC-SMD-CRYSTAL

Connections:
GND: C1.2, C2.2, C3.2, C4.2, C5.1, C6.2, C7.2, JP2.2, LED1.C, LED2.C, LED3.C, LED4.C, LED5.C, LED6.C, R1.2, S1.MINUS1, S1.MINUS2, U1.42, U1.TP (49), X1.P$2 (GROUND2), X1.P$4 (GROUND4)
unnamed: C2.1, U1.26, X1.P$3
unnamed: C1.1, U1.25, X1.P$1
unnamed: R1.1, U1.33
unnamed: R4.2, U1.2
unnamed: LED2.A, R4.1
unnamed: LED3.A, R5.1
unnamed: LED4.A, R6.1
unnamed: LED5.A, R7.1
unnamed: LED6.A, R8.1
unnamed: R3.2, U1.1
unnamed: LED1.A, R3.1
unnamed: R5.2, U1.3
unnamed: R6.2, U1.4
unnamed: R7.2, U1.5
unnamed: R8.2, U1.6
RFN: ANT-N.IN1, ANT-N.IN2, ANT-N.IN3, U1.30
RFP: ANT-P.IN1, ANT-P.IN2, ANT-P.IN3, U1.29
RST: C5.2, JP1.1, R2.1, U1.40
TEST: JP1.2, U1.39
VCC: C3.1, JP2.1, L1.1, R2.2, S1.PLUS, U1.8, U1.22, U1.34, U1.41, U1.45
VCCRF: C6.1, C7.1, L1.2, U1.27, U1.28, U1.31, U1.32
VCORE: C4.1, U1.7

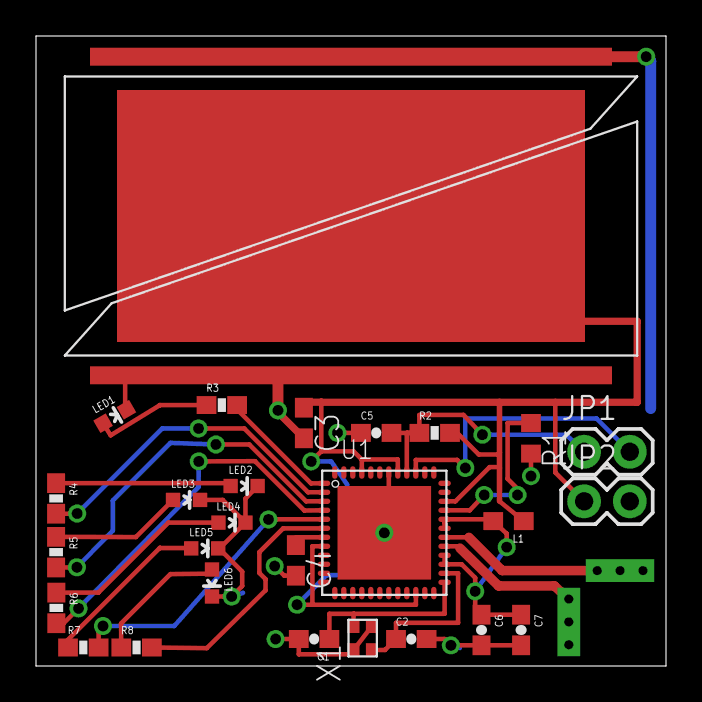
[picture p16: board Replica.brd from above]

Board: 2 copper layers, 35.0 x 35.0 mm, 29 parts (0 on the bottom side), 23 nets.

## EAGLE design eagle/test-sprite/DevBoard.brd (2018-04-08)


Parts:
ANT-N: ANTENNA
ANT-P: ANTENNA
C1, C2: 27pF; 0603-CAP
C3, C4: 470nF; C0603
C5, C8: 2.2nF; 0603-CAP
C6, C9, C11: 100nF; 0603-CAP
C7, C10: 10nF; 0603-CAP
C12: 220nF; 0603-CAP
C13: 4.7uF; 0603-CAP
JP1, JP2, JP3, JP4: M02PTH; 1X02
L1: 12 nH; 0603
LED1: LED0603; LED-0603
R1: 56K; R0603
R2: 47K; 0603-RES
R3, R4: 4.7K; 0603-RES
R5: 270R; 0603-RES
S1: TASC
U1: CC430F5137; RGZ48
U2: HMC5883LSMD; 16LPCC
U3: ITG-3200; QFN-24
X1: 26 MHz; ABM11_CERAMIC-SMD-CRYSTAL

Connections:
GND: C1.2, C2.2, C3.2, C4.2, C5.1, C6.2, C7.2, C8.2, C9.2, C10.2, C11.2, C13.2, JP1.2, LED1.C, R1.2, S1.MINUS1, S1.MINUS2, U1.42, U1.TP (49), U2.9 (GND), U2.11 (GND), U3.1 (CLKIN), U3.9 (AD0), U3.11 (RESV-G), U3.18 (GND), X1.P$2 (GROUND2), X1.P$4 (GROUND4)
unnamed: C2.1, U1.26, X1.P$3
unnamed: C1.1, U1.25, X1.P$1
unnamed: R1.1, U1.33
unnamed: C4.1, U1.7
unnamed: C12.1, U2.8 (SETP)
unnamed: C12.2, U2.12 (SETC)
unnamed: C13.1, U2.10 (C1)
unnamed: C8.1, U3.20 (CPOUT)
unnamed: C9.1, U3.10 (REGOUT)
unnamed: R5.2, U1.5
unnamed: LED1.A, R5.1
RFN: ANT-N.IN1, ANT-N.IN2, ANT-N.IN3, U1.30
RFP: ANT-P.IN1, ANT-P.IN2, ANT-P.IN3, U1.29
RST: C5.2, JP2.1, R2.1, U1.40
RXD: JP3.2, U1.12
SCL: R4.1, U1.3, U2.1 (SCL), U3.23 (SCL)
SDA: R3.1, U1.2, U2.16 (SDA), U3.24 (SDA)
TEST: JP2.2, U1.39
TXD: JP3.1, U1.11
VCC: C3.1, C10.1, C11.1, JP1.1, JP4.2, L1.1, R2.2, R3.2, R4.2, U1.8, U1.22, U1.34, U1.41, U1.45, U2.2 (VDD), U2.4 (S1), U2.13 (VDDIO), U3.8 (VLOGIC), U3.13 (VDD)
VCCRF: C6.1, C7.1, L1.2, U1.27, U1.28, U1.31, U1.32
VSOLAR: JP4.1, S1.PLUS


Board: 2 copper layers, 35.0 x 35.0 mm, 31 parts (0 on the bottom side), 23 nets.

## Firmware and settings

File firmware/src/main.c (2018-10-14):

#include <msp430.h>
#include <stdio.h>
#include <stdlib.h>
#include <string.h>

#include "config.h"

#include "battery_mon.h"
#include "calc.h"
#include "cc430uart.h"
#include "drvr.h"
#include "fault.h"
#include "flashctl.h"
#include "gitrev.h"
#include "i2c.h"
#include "lsm.h"
#include "pins.h"
#include "proto.h"
#include "timer_a.h"
#include "ucs.h"
#include "wdt_a.h"

#ifdef ALWAYS_SAFEMODE
volatile uint8_t faults = FAULT_RECENT_POR | FAULT_SAFEMODE;
#else
volatile uint8_t faults = FAULT_RECENT_POR;
#endif

#define DEC_OR_ZERO(x) x = (x > 0) ? x - 1 : 0;

#ifdef DEBUG
unsigned char counter_debug = 0;
#endif
unsigned char counter_por = 15;
unsigned char counter_tx = 0;
unsigned char counter_lsm = 0;

const char* VERSION_STR = "Spinor DEBUG (" GIT_REV ")\r\n";
#ifdef NO_ACTUATE
char tx_msg[10];
#else
char tx_msg[7];
#endif

struct vec3_s global_omega;
struct vec3_s meas_alpha;
struct vec3_s torqued_alpha;
struct vec3_s temp_alpha;
uint16_t sleep_counter = 0;
uint8_t run_time = 0;

void tick(void);

static void init_core() {
    // WDT intervals 1/(10 kHz/512K) = 51.2 secs
    WDT_A_initWatchdogTimer(WDT_A_BASE, WDT_A_CLOCKSOURCE_ACLK,
                            WDT_A_CLOCKDIVIDER_512K);

    // Reference FLL to REFO and set MCLK, SMCLK -> 1 MHz
    UCS_initClockSignal(UCS_FLLREF, UCS_REFOCLK_SELECT, UCS_CLOCK_DIVIDER_1);
    UCS_initFLLSettle(1000, 1000000/UCS_REFOCLK_FREQUENCY);

    // VLO (10 kHz) -> ACLK
    UCS_initClockSignal(UCS_ACLK, UCS_VLOCLK_SELECT, UCS_CLOCK_DIVIDER_1);

    // Set the High-Power Mode Request Enable bit so LPM3 can be entered
    // with active radio enabled
    PMMCTL0_H = 0xA5;
    PMMCTL0_L |= PMMHPMRE_L;
    PMMCTL0_H = 0x00;

    setup_pins();
    WDT_A_start(WDT_A_BASE);
}

void sleep(uint16_t ms, unsigned short mode) {
    struct Timer_A_initUpModeParam params = {
        TIMER_A_CLOCKSOURCE_ACLK,
        TIMER_A_CLOCKSOURCE_DIVIDER_10,
        ms,
        TIMER_A_TAIE_INTERRUPT_DISABLE,
        TIMER_A_CCIE_CCR0_INTERRUPT_ENABLE,
        TIMER_A_DO_CLEAR,
        true};
    Timer_A_initUpMode(TIMER_A0_BASE, &params);
    __bis_SR_register(mode);
    sleep_counter += ms;
}

void deep_sleep(uint16_t ms) {
    sleep(ms, LPM3_bits);
}

static void blink(const uint16_t ms) {
    P3OUT |= BIT7;
    deep_sleep(50);
    P3OUT &= ~BIT7;
    deep_sleep(ms - 50);
}

static void blink_main() {
    while (1) blink(1000);
}

/**
 * Call this once after init_core(). After that, only from the PGOOD ISR.
 */
static void check_power() {
    P1IE &= ~BIT1; // Changing P1IES could result in extra interrupt
    if (P1IN & BIT1) {
        // PGOOD high, set interrupt to negative edge
        faults &= ~FAULT_POWER;
        P1IES |= BIT1;
        P1IE |= BIT1;
    } else {
        // PGOOD low, set interrupt to positive edge
        faults |= FAULT_POWER;
        P1IES &= ~BIT1;
        P1IE |= BIT1;
    }
}

static void init_debug() {
    blink(200);
    uart_begin(9600, SERIAL_8N1);
    uart_write(VERSION_STR, strlen(VERSION_STR));
}

void tick() {
#ifdef DEBUG
    DEC_OR_ZERO(counter_debug);
#endif
    DEC_OR_ZERO(counter_por);
    DEC_OR_ZERO(counter_tx);
    DEC_OR_ZERO(counter_lsm);

    if (counter_por == 0)
        faults &= ~FAULT_RECENT_POR;
}

static bool check_power_ok() {
    // Ignore FAULT_POWER if FAULT_MPPT is set
    return !(faults & FAULT_POWER) || (faults & FAULT_MPPT);
}

bool radio_precond() {
    return check_power_ok();
}

bool lsm_precond() {
    return !(faults & FAULT_SAFEMODE) && check_power_ok();
}

bool actuate_precond() {
    return lsm_precond() &&
        !(faults & FAULT_RECENT_POR) && !(faults & FAULT_LSM_SETUP);
}

int rand_int(int min, int incr) {
    return min + rand()/(RAND_MAX/incr);
}

/**
 * Determine whether to enter safe mode or not. Always enter safe mode, unless
 * system reset was caused by a whitelisted trigger.
 */
static bool check_enter_safemode() {
    switch (__even_in_range(SYSRSTIV, SYSRSTIV_PMMKEY)) {
        case SYSRSTIV_NONE:
            return false;
        case SYSRSTIV_BOR:
            return false;
        case SYSRSTIV_RSTNMI:
            return false;
        case SYSRSTIV_SVSL:
            return false;
        case SYSRSTIV_SVSH:
            return false;
        default:
            return true;
    }
}

int main() {
    init_core();
    if (check_enter_safemode()) {
        faults |= FAULT_SAFEMODE;
    }
    __enable_interrupt();
#ifdef DEBUG
    init_debug();
#endif
    if (setup_bat_monitor()) {
        start_bat_monitor();
    } else {
        faults |= FAULT_GPF;
    }
    check_power();

    while (true) {
        WDT_A_resetTimer(WDT_A_BASE);
        if (counter_tx == 0 && radio_precond()) {
            tx_msg[0] = 0;
            tx_msg[1] = (faults << 2) | (((batt_voltage - 127)>>6) & 0x03);
            tx_msg[2] = temp_measure;
            uint16_t global_val = (uint16_t) norm(&global_omega);
            tx_msg[3] = (uint8_t)(global_val >> 8);
#ifdef NO_ACTUATE
            struct vec3_s m_data;
            readMag(&m_data);
            tx_msg[4] = m_data.x >> 8;
            tx_msg[5] = m_data.x & 0xff;
            tx_msg[6] = m_data.y >> 8;
            tx_msg[7] = m_data.y & 0xff;
            tx_msg[8] = m_data.z >> 8;
            tx_msg[9] = m_data.z & 0xff;
#else
            tx_msg[4] = (uint8_t)(global_val & 0xFF);
            tx_msg[5] = (int8_t)(norm(&torqued_alpha) - norm(&meas_alpha));
            tx_msg[6] = (uint8_t)(run_time);
#endif
            run_radio();
            counter_tx = rand_int(20, 9);
#ifdef DEBUG
            char buf[32];
            snprintf(buf, sizeof(buf), "sleeping %d\r\n", counter_tx);
            uart_write(buf, strlen(buf));
#endif
        } else if (counter_lsm == 0 && lsm_precond()) {
            run_lsm(&meas_alpha);
            counter_lsm = 15;
#ifdef DEBUG
        } else if (counter_debug == 0) {
            char buf[32];
            snprintf(buf, sizeof(buf), "faults: 0x%x\r\n", faults);
            uart_write(buf, strlen(buf));
            snprintf(buf, sizeof(buf), "vbat: %u\r\n", batt_voltage);
            uart_write(buf, strlen(buf));
            snprintf(buf, sizeof(buf), "temp: %u\r\n", temp_measure);
            uart_write(buf, strlen(buf));
            counter_debug = 3;
#endif
        } else if (actuate_precond()) {
#ifndef NO_ACTUATE
            run_lsm(&temp_alpha); // temp_alpha needed but not actually used
            struct vec3_s m_data;
            readMag(&m_data);
            struct vec3_s g_data;
            readGyro(&g_data);
            uint8_t axis;
            int8_t power;
            magnetorquer_out(m_data, g_data, &axis, &power);
#ifdef DEBUG
            char buf[32];
            snprintf(buf, sizeof(buf), "axis %u power %d\r\n", axis, power);
            uart_write(buf, strlen(buf));
#endif
            run_time = run_actuation(axis, power, &torqued_alpha);
#endif
        }

        // Wait at least 1 second before looping.
        if (sleep_counter < 1000) {
            deep_sleep(1000 - sleep_counter);
        }

        for (; sleep_counter >= 1000; sleep_counter -= 1000) {
            // Long sleeps should tick to keep timing reasonable.
            tick();
        }
        sleep_counter = 0;
    }
}

void __interrupt_vec(TIMER0_A0_VECTOR) isr_timer_a0() {
    LPM3_EXIT;
}

void __attribute__((critical)) __interrupt_vec(PORT1_VECTOR) isr_p1() {
    switch (__even_in_range(P1IV, P1IV_P1IFG7)) {
    case P1IV_P1IFG1:
        check_power();
        LPM3_EXIT; // exit early from pending delays
        break;
    default:
        break;
    }
}

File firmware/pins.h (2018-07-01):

/**
 * Copyright (c) 2018 STAC <stac.berkeley.edu>
 * 
 * Author: Aviral Pandey
 * Creation date: 07/01/2018
 */

#ifndef _PINS_H
#define _PINS_H

#include <stdint.h>

#define __SPRITE_VERSION_2_0__  1

// Enable pseudo-pin interrupts on P3
#define __ENABLE_P3_PIN_INTERRUPTS__  1

// UART
#define pinUARTmap()      P1MAP6 = PM_UCA0TXD; P1MAP5 = PM_UCA0RXD
#define pinUARTconfig()   P1SEL |= BIT6 | BIT5      // Set P1.6 and P1.5 to USCI Mode
// I2C
#define pinI2Cmap()       P1MAP4 = PM_UCB0SCL; P1MAP3 = PM_UCB0SDA
#define pinI2Cconfig()    P1SEL |= BIT3 | BIT4      // Set P1.4 and P1.3 to USCI function
// SPI
#define pinSPImap()       P1MAP0 = PM_UCB0SIMO; P1MAP1 = PM_UCB0SOMI; P1MAP2 = PM_UCB0CLK
#define pinSPIconfig()    P1SEL |= BIT0 | BIT1 | BIT2  // Set P1.0, P1.1 and P1.2 to USCI function

#define NOT_A_PORT 0
#define NOT_A_PIN 0
#define NOT_ON_TIMER 0
#define NOT_ON_ADC 0xFF

// Ports
enum{
  P1 = 1,
  P2,
  P3,
  PJ
};

// Timers
enum{
  T0A0,
  T0A1,
  T0A2,
  T0A3,
  T0A4,
  T1A0,
  T1A1,
  T1A2
};

// ADC channels
// [Avi] Updated on 7/1, seemed incorrect before
static const uint8_t A0 = 0;
static const uint8_t A1 = 1;
static const uint8_t A2 = 2;
static const uint8_t A3 = 3;
// static const uint8_t A4 = 4;
// static const uint8_t A5 = 5;        // Connected to NTC
// static const uint8_t A10 = 128 + 10; // special. This is the internal temp sensor
static const uint8_t Atemp = 0b1010; // special. This is Vcc/2

// On-board LED
// Da Fuq are these? 
#define ONBOARD_LED 23
#define LED      ONBOARD_LED
#define INIT_ONBOARD_LED()    P3DIR |= BIT7; P3OUT &= ~BIT7
// ADC resolution
#define ADC_RESOLUTION  0xFFF

// LD-BOARD definitions
#define HGM     20
#define LNA_EN  19
#define PA_EN   18

const uint16_t digital_pin_to_pmap[] = {
	(uint16_t) &P1MAP0, 
	(uint16_t) &P1MAP1,
  (uint16_t) &P1MAP2,
  (uint16_t) &P1MAP3,
  (uint16_t) &P1MAP4,
  (uint16_t) &P1MAP5,
  (uint16_t) &P1MAP6,
  (uint16_t) &P1MAP7,
	(uint16_t) &P2MAP0,
  (uint16_t) &P2MAP1,
  (uint16_t) &P2MAP2,
  (uint16_t) &P2MAP3,
  (uint16_t) &P2MAP4,
  (uint16_t) &P2MAP5,
  (uint16_t) &P2MAP6,
  (uint16_t) &P2MAP7,
	(uint16_t) &P3MAP0,
  (uint16_t) &P3MAP1,
  (uint16_t) &P3MAP2,
  (uint16_t) &P3MAP3,
  (uint16_t) &P3MAP4,
  (uint16_t) &P3MAP5,
  (uint16_t) &P3MAP6,
  (uint16_t) &P3MAP7  // On-board LED
};

const uint16_t port_to_input[] = {
	NOT_A_PORT,
	(uint16_t) &P1IN,
	(uint16_t) &P2IN,
	(uint16_t) &P3IN,
	(uint16_t) &PJIN
};

const uint16_t port_to_output[] = {
	NOT_A_PORT,
	(uint16_t) &P1OUT,
	(uint16_t) &P2OUT,
	(uint16_t) &P3OUT,
	(uint16_t) &PJOUT
};

const uint16_t port_to_dir[] = {
	NOT_A_PORT,
	(uint16_t) &P1DIR,
	(uint16_t) &P2DIR,
	(uint16_t) &P3DIR,
	(uint16_t) &PJDIR
};

const uint16_t port_to_ren[] = {
	NOT_A_PORT,
	(uint16_t) &P1REN,
	(uint16_t) &P2REN,
	(uint16_t) &P3REN,
	(uint16_t) NOT_A_PORT  //No PJREN
};

const uint16_t port_to_sel[] = {
	NOT_A_PORT,
	(uint16_t) &P1SEL,
	(uint16_t) &P2SEL,
	(uint16_t) &P3SEL,
	(uint16_t) NOT_A_PORT  // No PJSEL,
};

const uint16_t port_to_pmap[] = {
	NOT_A_PORT,	/* PMAP starts at port P1 */
	(uint16_t) &P1MAP0,
	(uint16_t) &P2MAP0,
	(uint16_t) &P3MAP0,
	NOT_A_PORT  // No PJMAP0
};

const uint8_t digital_pin_to_timer[] = {
	T0A0,         /* P1.0 - note: A0 output cannot be used with analogWrite */
	T0A1,         /* P1.1 */
	T0A2,         /* P1.2 */
	T0A3,         /* P1.3 */
	T0A4,         /* P1.4 */
	NOT_ON_TIMER, /* P1.5 */
	NOT_ON_TIMER, /* P1.6 */
	NOT_ON_TIMER, /* P1.7 */
	NOT_ON_TIMER, /* P2.0 */
	NOT_ON_TIMER, /* P2.1 */
	NOT_ON_TIMER, /* P2.2 */
	NOT_ON_TIMER, /* P2.3 */
	NOT_ON_TIMER, /* P2.4 */
	NOT_ON_TIMER, /* P2.5 */
	NOT_ON_TIMER, /* P2.6 */
	NOT_ON_TIMER, /* P2.7 */
  NOT_ON_TIMER, /* P3.0 */
	T1A0,         /* P3.1 - note: A0 output cannot be used with analogWrite */
	T1A1,         /* P3.2 */
	T1A2,         /* P3.3 */
  NOT_ON_TIMER, /* P3.4 */
  NOT_ON_TIMER, /* P3.5 */
  NOT_ON_TIMER, /* P3.6 */
	NOT_ON_TIMER  /* P3.7 -> ONBOARD_LED */
};

const uint8_t digital_pin_to_port[] = {
	P1,           /* P1.0 */
	P1,           /* P1.1 */
	P1,           /* P1.2 */
	P1,           /* P1.3 */
	P1,           /* P1.4 */
	P1,           /* P1.5 */
	P1,           /* P1.6 */
	P1,           /* P1.7 */
	P2,           /* P2.0 */
	P2,           /* P2.1 */
	P2,           /* P2.2 */
	P2,           /* P2.3 */
	P2,           /* P2.4 */
	P2,           /* P2.5 */
	P2,           /* P2.6 */
	P2,           /* P2.7 */
	P3,           /* P3.0 */
	P3,           /* P3.1 */
	P3,           /* P3.2 */
  P3,           /* P3.3 */
  P3,           /* P3.4 */
  P3,           /* P3.5 */
  P3,           /* P3.6 */  
	P3            /* P3.7 -> ONBOARD_LED */
};
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

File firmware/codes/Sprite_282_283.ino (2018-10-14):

#include <SpriteRadio.h>

static unsigned char prn282[64] = {
  0b10101110, 0b00100000, 0b10101110, 0b00101110, 0b10011100, 0b00100011, 0b00011101, 0b00010000,
  0b10001001, 0b11001001, 0b00101110, 0b01000011, 0b10010100, 0b11100010, 0b00001101, 0b10010111,
  0b10101010, 0b01100000, 0b00101001, 0b11100111, 0b00011010, 0b11001011, 0b00110101, 0b01110010,
  0b11100111, 0b11110100, 0b10111011, 0b11001011, 0b11110100, 0b11100010, 0b11001110, 0b00001100,
  0b00110111, 0b11000011, 0b10101110, 0b00000101, 0b10110011, 0b00010110, 0b00010000, 0b10001101,
  0b10010110, 0b00111111, 0b01001001, 0b01111101, 0b10011111, 0b10111111, 0b00011011, 0b01011000,
  0b11011000, 0b01110000, 0b10110111, 0b01001110, 0b10101100, 0b01001110, 0b00011000, 0b01011001,
  0b00110101, 0b00011110, 0b00110010, 0b01100101, 0b01000011, 0b11001010, 0b11011010, 0b11001110
};

static unsigned char prn283[64] = {
  0b10100011, 0b11000010, 0b10000011, 0b01001010, 0b00001010, 0b01001111, 0b01110100, 0b11110000,
  0b11110100, 0b01011111, 0b11010110, 0b00010110, 0b11101111, 0b00010001, 0b11011111, 0b11101011,
  0b00010100, 0b11100001, 0b01001011, 0b10000000, 0b01100000, 0b00010000, 0b10011110, 0b00111001,
  0b01000101, 0b11111100, 0b11010000, 0b01111011, 0b01111011, 0b00011010, 0b00001111, 0b01001011,
  0b01011111, 0b10011111, 0b10010110, 0b00111111, 0b11011001, 0b10001110, 0b11100110, 0b01000010,
  0b01001011, 0b11110001, 0b00101000, 0b11110110, 0b01010010, 0b10100110, 0b00011011, 0b11001100,
  0b11100100, 0b11101011, 0b00111001, 0b00001010, 0b00101000, 0b10100101, 0b11100010, 0b11001000,
  0b10000000, 0b00011000, 0b01010111, 0b01001111, 0b01101010, 0b00001111, 0b10101000, 0b01111110
};

SpriteRadio m_radio = SpriteRadio(prn282, prn283);

void setup() {
  pinMode(5, OUTPUT);
  m_radio.txInit();
};

void loop() {
  digitalWrite(5, HIGH);
  m_radio.transmit("Test\n", 5);
  digitalWrite(5, LOW);
};

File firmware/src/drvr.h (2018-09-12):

#pragma once

#include "lsm.h"

enum Driver {
    XAXIS = 0, // EN_3, Spiral inductor
    YAXIS = 1, // EN_2, Back top
    ZAXIS = 2, // EN_1, Back left
};

uint8_t run_actuation(uint8_t axis, int8_t power, struct vec3_s data[static 1]);
void setup_pwm(void);

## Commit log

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2018-04-08 gerbers for DevBoard & Programmer replicas in folder. Use latest versions
    [Programmer.brd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]
2018-04-11 generated .step for DevBoard & altium projs from EAGLE
    [ABM11.PCBLIB, ABM11.PrjPcb, ABM11.SCHLIB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]
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2018-04-14 updated BOM for sprite DevBoard replica
    [BOM.xlsx]
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2018-05-27 Reorganize production files
    - Remove ZIP files
    - Move their expanded contents to gerbers/
    [DevBoard.GBL, DevBoard.GBO, DevBoard.GBS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]
2018-05-29 Remove sample files from other repositories
    [Antenna.brd, Antenna.sch, Mainbaord.brd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]
2018-05-29 updated README.rst and added Attitude sprite to eagle/final-sprite
    [BOM.xlsx, DevBoard.brd, DevBoard.sch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]
2018-06-01 issues with board version
2018-06-06 merged final-sprite changes into master branch
    [sprite.brd, sprite.sch]
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2018-06-07 More progress on COIL12
    [sprite.brd, sprite.sch]
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2018-06-07 Giving Kevin more space
    [sprite.sch]
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2018-06-07 changed passives to 0402 in schematic
    [sprite.brd, sprite.sch]
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2018-06-07 Remove blank sheet 2
    [sprite.sch]
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2018-06-10 consistent board, pre-renumbering passives
    [sprite.brd, sprite.sch]
2018-06-10 Updated schematic with DRV8837 drivers
    [sprite.brd, sprite.sch]
2018-06-10 Remove unused fault nets
    [sprite.brd, sprite.sch]
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2018-06-10 started layout and fixed R0402 packages
    [sprite.brd, sprite.sch]
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2018-06-11 Placed all components, probably
    [sprite.brd, sprite.sch]
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2018-06-11 hand routed RF_P and RF_N
    [sprite.brd]
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2018-06-11 successful autoroute 2 blind capability 69 vias
    [sprite.brd]
2018-06-11 did most of the long traces
    [sprite.brd, sprite.sch]
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2018-06-11 routed some more routes
    [sprite.brd, sprite.sch]
2018-06-12 routed all traces, need to do GND and VCC
    [sprite.brd, sprite.sch]
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2018-06-13 Add straight edge RS solar cell drawing
    [TrisolX RS.dxf]
2018-06-13 Move dev board model
    [DevBoard_stp.step]
2018-06-13 moved all 3 drivers to the bottom side, removed the need for using interlayers and decreased the total number of vias
    [sprite.brd]
2018-06-13 added new trisol footprint to layout
    [sprite.brd, sprite.sch]
2018-06-14 Finishing up more of the Layout
    [sprite.brd, sprite.sch]
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2018-06-16 Fix inductor
    [sprite.kicad_pcb, sprite.sch]
2018-06-16 Remove extra test point
    [sprite.kicad_pcb, sprite.sch]
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2018-06-17 some changes to KiCAD version of things
    [sprite.kicad_pcb]
2018-06-17 Fix footprints and layout
    [sprite.kicad_pcb, sprite.sch]
2018-06-17 More routing, removed some vias from the bottom layer
    [sprite.kicad_pcb]
2018-06-17 spiral inductor that can actually be fab'd
    [sprite.kicad_pcb]
2018-06-17 Add layer 3 fill and ENIG note
    [sprite.kicad_pcb]
2018-06-17 more routes fixed, removed some vias
    [sprite.kicad_pcb, sprite.sch]
2018-06-17 Fixing pgood renaming
    [sprite.sch]
2018-06-17 Fix silkscreen
    [sprite.kicad_pcb]
2018-06-17 Remove pours over PCB inductor
    [sprite.kicad_pcb]
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2018-06-18 updated resistitator values again
    [sprite.sch]
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2018-06-27 Add note about tenting vias
    [sprite.kicad_pcb]
2018-06-29 Update schematic title block matter
    [sprite.sch]
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2018-06-29 Update values from schematic
    [sprite.kicad_pcb]
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2018-07-01 Track core fixes needed for sprite_main to work
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2018-07-01 Fix inductor test points
    [sprite.kicad_pcb, sprite.sch]
2018-07-01 Fix SpritePin footprint
2018-07-02 Fix size of R10
    [sprite.kicad_pcb, sprite.sch]
2018-07-02 Reduce solar cell rectangle size
    [sprite.kicad_pcb]
2018-07-02 Add via fill note
    [sprite.kicad_pcb]
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2018-07-02 did some nephew tier routing, but added optional 0ohm resistor between Pgood and RST
    [sprite.kicad_pcb, sprite.sch]
2018-07-02 Clarify via fill requirement
    [sprite.kicad_pcb]
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2018-07-05 fixed compilation issues part 2
    [drvr.c, drvr.h, main.c]
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2018-07-05 fixing broken pins.h file
    [drvr.c, main.c, pins.c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]
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2018-07-06 Replace delayMicroseconds() with LPM0 sleep
    [main.c]
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2018-07-08 uart code that doesn't work
    [cc430uart.c, i2c.c, lsm.c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]
2018-07-08 minor modifications to i2c but still not workign
    [cc430uart.c, i2c.c, lsm.c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]
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2018-07-09 Fix sleep LPM
    ACLK is disabled in LPM4, so timer wakeup from LPM4 isn't supposed to
    work. It did for some reason, but just to be safe change to LPM3.
    [main.c]
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2018-07-10 Give FLL time to settle
    This was causing problems with UART right after startup.
    [main.c]
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2018-07-14 fixing compilation issue and removing executable-ness from some src files
    [pins.h]
2018-07-22 Fixed i2c and lsm transactions
    [i2c.c, lsm.c, lsm.h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]
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2018-07-31 Set interrupts correctly
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2018-08-05 Fix driver test code
    [drvr.c]
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2018-08-18 Update radio register comments
    While here, remove the ones that we didn't check and potentially
    misleading ones. Better to check against datasheet and add them back
    when we need them.
    [radio.c]
2018-08-23 added in new super cap
    [sprite.kicad_pcb, sprite.sch]
2018-08-23 Save supercap footprint in sprite library
    [sprite.kicad_pcb, sprite.sch]
2018-08-23 Dump in a few more supercaps
    [sprite.kicad_pcb, sprite.sch]
2018-08-24 added more caps and moved a couple traces
    [sprite.kicad_pcb, sprite.sch]
2018-08-24 routes fixed, no DRC violations, 11 new caps
    [sprite.kicad_pcb]
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2018-08-25 fixed silkscreen
2018-08-25 WIP routing w slot
    [sprite.kicad_pcb]
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2018-08-25 Added edge cut. Final version probably
    [sprite.kicad_pcb]
2018-08-25 Remove silkscreen logo on back
    [sprite.kicad_pcb]
2018-08-25 Line up slot on grid
    [sprite.kicad_pcb]
2018-08-25 Remove back silkscreen logo
    [sprite.kicad_pcb]
2018-08-25 Add more slot margin and move top logo
    [sprite.kicad_pcb]
2018-08-25 Fix unconnected
    [sprite.kicad_pcb]
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2018-09-09 fixing lsm issue by resetting lsm at every call to setup()
    [lsm.c]
2018-09-10 fixing lsm magnetometer code, by reseting the ctrl_reg3_m
    [lsm.c]
2018-09-10 Stop rebooting magnetometer
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2018-09-12 Check for MPPT failure
    Report inconsistencies between PGOOD and measured battery voltage.
    [battery_mon.c, main.c]
2018-09-12 Fix UART signedness
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2018-09-12 Add missing ifdef DEBUG
    [lsm.c]
2018-09-12 Do not attempt to actuate if LSM setup fails
    [main.c]
2018-09-13 Flip UMAC connectors and offset coil pad
    [sprite.kicad_pcb]
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2018-09-13 Update footprints for non-slotted board
    [sprite.kicad_pcb]
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2018-09-14 Fix redundant pin setup
    [pins.c]
2018-09-14 Set GPF if ADC setup fails
    [battery_mon.c, main.c]
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2018-09-14 Update notes to plug instead of fill vias
    [sprite.kicad_pcb]
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2018-09-15 Cap board respin for thinner profile
    [DevBoard.kicad_pcb, DevBoard.sch, sprite.kicad_pcb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]
2018-09-15 Cap board repsin with all nets connected
    [sprite.kicad_pcb]
2018-09-15 Fix edge cuts
    [sprite.kicad_pcb]
2018-09-15 Add via to fix layer 3 fill
    While here connect antenna pins to silence unconnected warning.
    [sprite.kicad_pcb]
2018-09-16 moving around traces to create room for the center spiral inductor
    [sprite.kicad_pcb]
2018-09-16 Prepare layout for spiral inductor
    [sprite.kicad_pcb]
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2018-09-17 updated pcb with spots for 6 more caps
    [sprite.kicad_pcb, sprite.sch]
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2018-09-19 Fix edge cut
    [sprite.kicad_pcb]
2018-09-23 fixing some compilation issues
    [lsm.c]
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2018-09-23 fixed lsm.h and fixed incorrect directory for firmware download
    [lsm.h]
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2018-09-25 added /100 to data reduce effect of noise
    [lsm.c]
2018-09-26 fixed printing
2018-10-12 fixed calls to run_actuations
    [main.c]
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2018-12-20 Added accurate baselines for m and g
    [ISS001.csv]
2018-12-21 Ran iss_loc.py script for 9 hours and stored data into iss_loc_data_1545365126.csv. iss_loc_data_1545364972.csv is just a test file
    [iss_loc_data_1545364972.csv, iss_loc_data_1545365126.csv]
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2018-12-23 Changed gyro data to be in radians/s instead of deg/s
    [ISS001.csv, full_1545365126.csv, iss_loc_data_1545364972_full.csv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]
2019-01-01 added method for unique random init of gyro data - still axis=1 issue
    [full_1545365126.csv]
2019-01-01 Added offset to mag_x. Full_ files have gyro data that is the same for all rows. fullunique_ files have gyro data that is unique to each row.
    [full_1545365126.csv, fullunique_1545365126.csv]
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2019-04-20 fixing compatibility issue with schematic
    [sprite.sch]

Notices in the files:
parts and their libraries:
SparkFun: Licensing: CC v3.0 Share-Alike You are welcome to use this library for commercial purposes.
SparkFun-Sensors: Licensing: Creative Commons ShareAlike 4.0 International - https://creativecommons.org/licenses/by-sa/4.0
